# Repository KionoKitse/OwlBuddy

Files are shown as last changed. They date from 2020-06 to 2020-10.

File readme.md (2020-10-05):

### Description  
P09_00_00 OwlBuddy
This project is a simple modify but not repurpose hack. I'm taking a mechanical owl timer that doesn't work very well and converting it into a digital animatronics timer.  
Features
 * Adjustable timing between 1-60 min
 * Servo motion for head movement
 * Detection of timing adjustment
 * Audio feedback
 * LED strobe beacon
 * Battery powered
 * Charge level monitoring
 * Integrated USB charging
 * Automatic sleep and wakeup

### Notes to user
 * Project documented at https://kionokitse.wordpress.com/owlbuddy
 * In development
 
### Hardware
 * Arduino Pro Mini clone ATmega328 5V
 * Micro servo Tower Pro SG90
 * Micro stepper motor
 * High output LED
 
### Progress log 
 * 2020-06-15 Initial project idea 
 * 2020-06-16 Deciding on features and components
 * 2020-06-16 Ordering components
 * 2020-06-16 Initial design sketches
 * 2020-06-17 Ordering components
 * 2020-06-17 Testing LEDs
 * 2020-06-17 Solder stepper motor
 * 2020-06-17 CAD design
 * 2020-06-17 Gear train 
 * 2020-07-04 Redesign CAD P09_00_01
 * 2020-07-04 Start writing software
 * 2020-07-13 Finished 3D printing main components
 * 2020-07-13 Got the VCC readings from the pro mini
 * 2020-07-13 Modify servo for continuous rotation 3.3kOhm resistors
 * 2020-07-13 Testing drive servo with low battery (didn't work)
 * 2020-07-13 Testing direct drive with Arduino pins for the servo motor (didn't work)
 * 2020-07-13 Possible to drive motor using battery leads
 * 2020-07-13 Remove H bridge from SG90 (117L 929 datasheet not found)
 * 2020-07-13 Mapping H bridge pins from SG90
 * 2020-07-13 Modify owl base to accept mini USB adapter
 * 2020-07-14 Probing H bridge found working pinout still a couple unknown pins
 * 2020-09-22 Testing hall effect sensor based encoder 
 * 2020-09-22 Hall encoder results look noisy filtering is very difficult maybe need another approach
 * 2020-09-22 Search mode is the best filter mode so far average filter offsets results slightly
 * 2020-09-22 Inconsistent resistance results in some sections moving faster requiring different filter settings
 * 2020-09-22 Should consider adjustable filter settings
 * 2020-09-26 Testing the idea of adding magnets to the internal gears of the servo
 * 2020-09-27 Testing using metal rods instead of magnets in internal gears
 * 2020-09-27 Tests worked but the process damages the gears not a (feasible option)
 * 2020-09-27 Revisiting the two potentiometer design with trace reinforcement
 * 2020-09-29 Testing dual pot results seem promising
 * 2020-09-29 For the dual pot design I'm noticing when pin A0 is floating it closely resembles pin A1 (not floating) but with more variance
 
### What's next
 * Write a filter to sort out which potentiometer to read from
 * Test wake up from sleep using potentiometer
 * Design layout
 * Test pro mini pins
 * Need to reduce the battery until I can find the min voltage that will drive this project
 
### Function
 * Hardware is asleep 
 * User sets owl time
 * Moving the head will trigger the wakeup command (maybe I need a switch here)
 * Arduino checks the battery voltage if the voltage is low the LED will blink rapidly
 * Timer waits for a few seconds before reading the potentiometer 
 * Timer reads time value
 * Beacon is activated for a few seconds
 * Drive motor goes back to zero then negative whatever value was put include
 * Drive motor goes back to set value
 * Beacon is activated again once the timer starts
 * Arduino goes to sleep
 * Arduino wakes up and moves the drive motor every minute towards zero
 * Arduino also remembers the last set value
 * If the user adjusts the time while the timer is activated the timer will adjust the time accordingly and blink the LED to acknolegde
 * Once the timer goes to zero owl moves 180 then -180 twice before returning to zero
 * During this time the beacon is activated
 * Afterwards the Arduino goes to sleep
 
### Notebook
 * Battery source Li-Po, Li-ion, or Ni-Mh. Ni-Mh has a similar capacity to Li-ion and weight isn't an issue. I already have these batteries and a simple USB charger for them. Size is a little big but it can fit more or less.  
 
 * Sum of squares function that seems to work well https://www.thoughtco.com/sum-of-squares-formula-shortcut-3126266
 * Direct control of mini stepper motor			https://www.youtube.com/watch?v=MaByP2w_vtA
 * Idea for slip ring power for LED strobe		https://gizmoplans.com/product/wind-turbine-slip-rings/
 * Interesting page on li-po charging			https://electronics-project-hub.com/arduino-lithium-ion-battery-charger/
 * CAD for SG90 Servo							https://www.thingiverse.com/thing:787942
 * Putting Arduino to sleep with watchdog		https://learn.adafruit.com/low-power-wifi-datalogging/power-down-sleep
 * Adjust VCC pin reading (didn't use)    		https://forum.arduino.cc/index.php?topic=435065.0 
 * Use VCC pin to read voltage		        	https://provideyourown.com/2012/secret-arduino-voltmeter-measure-battery-voltage/
 
### Next Blog Post
2020-09-29 <font color="63C0EC"><b>P09_00_00 Dual pot design</b></font>
Currently the big sticking point of this project is determining and controlling the head position. I have an SG90 servo that is directly coupled to the head and fixed to the body. I want the head to be able to rotate 360 degrees to allow the user to set a time between 1-60 min. The SG90 servo is only rated to 180 degrees of rotation so I've removed the limits. This allows me to drive the servo as essentially a gear head motor but removes the feedback loop. I've tried a lot of different ideas from hall effect sensors to pulse counting and stacked potentiometers. What I'm doing now is that stack potentiometer idea again. It was one of the first ideas I tried but I noticed that after a few days the potentiometers started bugging out. After disassembly I noticed that the wiper had worn down traces in the sections of the potentiometers that it was not designed to be in. The silver traces did not have any protection against the mechanical abrasion of the wiper. 
>>>IMAGE<<<
The idea was abandoned because I did not see any good way to prevent this from happening and still get continuous rotation. After a lot of trying other stuff it seemed that the dual potentiometer idea was the only idea that had shown some promise. Revisiting the idea I decided that maybe the best option was to protect the traces. For this, I've decided to use a bit of super glue to lay down a protective layer over the silver traces. I'm not sure how well this will stand up to the repeated abrasion but I'm keen to see if it will work. Here is an image of the dual potentiometer I've put together. The two potentiometers have their wipers in opposing positions so when one potentiometer is in the invalid range the other will be in it's valid range.
>>>IMAGE<<< 
<font color="63C0EC">Category:</font> Engineering
<font color="63C0EC">Tags:</font> Animatronics, Arduino, Engineering, Mechatronics, P09_00_00, Timer
<a href="https://kionokitse.wordpress.com/owlbuddy/">Project Page</a>

2020-09-29 <font color="63C0EC"><b>P09_00_00 Dual pot output</b></font>
Recently I had a chance to test the new dual potentiometer design. The results are looking promising but not quite what I had been expecting. One of the effects of coating the traces in super glue is that they are no longer conductive. This is a good thing because if it was conductive, the power would short between the contacts. I hadn't thought of that but note to self: super glue is non-conductive. The other effect that was unexpected is that it seems that a floating pin (no signal) will mirror a non-floating pin on the Arduino. I'm not sure under what cases this is true but in my case it was. On my setup I had A0 reading potentiometer A (PotA) and A1 reading potentiometer B (PotB). When PotA was in the invalid region and thus acting as a floating pin I noticed that it mirrored the results seen on PotB. The same happens if PotB is in the invalid region and PotA is in the valid region. Originally I though that maybe I had some sort of short that was connecting the output of PotA and PotB but that was not the case. If I move PotA into the valid region and transverse the valid region on PotB it's clear to see that there is no connection between them. In effect, this means that I will always be reading two values from the potentiometers that on the surface look valid. Here is a graph of two periods or 520 degrees of rotation.
>>>IMAGE<<<
It's not clear which sensor is in the valid region and which sensor is in the invalid region. One thing I noticed though was that it was possible to distinguish the two based on the amount of noise in the data. If a pin is floating then it's likely that all the data that is coming in in noise. Not quite what is happening here but with noise there tends to be quite a lot of variance compare to a set pin. When I look closer and the signal data it's easy to see which sensor is actually in the valid region.
>>>IMAGE<<<
>>>IMAGE<<<
<font color="63C0EC">Category:</font> Engineering
<font color="63C0EC">Tags:</font> Animatronics, Arduino, Engineering, Mechatronics, P09_00_00, Timer
<a href="https://kionokitse.wordpress.com/owlbuddy/">Project Page</a>

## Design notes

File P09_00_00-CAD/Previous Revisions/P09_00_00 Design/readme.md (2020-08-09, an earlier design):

### Overview:
__Name:__ P09_00_00 CAD Design <br>
__Software Version:__ FreeCAD 0.15 <br>
__Notes:__ Design superseded by P09_00_01 <br>
__Comments:__ This design did not work well. The gears were not supported well and caused pinching which was too much friction for the servo. Additionally the design was somewhat restrictive in only being able to rotate 360 degrees.

### Description:
This design is the first iteration of P90_00_00. It calls for one SG90 servo to control the owl head movement and one micro stepper motor for the beacon motion. With additional gearing the servo action is extended to a full 360 degrees of motion. The timer setting are directly read from the servo potentiometer.  

### Files:
 * __Assembly:__ The parts aligned to check for interference
 * __BeaconLens:__ The red lens that covers the LED on top of the owl's head
 * __LEDMount:__ The mounting part that mates the stepper motor with the LED
 * __StepperMast:__ Part that holds the stepper motor vertically and mates to the BeaconBase to ensure the mast is centered
   * R2: Redesigned with a hallow center for passing wires though the BeaconBase and DriveGear  
 * __BeaconBase:__ Platform for beacon in the owl timer head
   * R2: Design modified for attaching directly to the drive gear. R1 design was flawed
 * __DriveGear:__ Main drive gear for owl head motion connected to servo motor in owl body
   * R2: Reduced the gear module
 * __ServoGear:__ Gear that is placed on servo head to drive the head action
   * R2: Reduced the gear module
 * __MainFrame:__ The main frame component where the servo is attached to the owl body
   * R2: Redesigned with the servo motor at an angle for better access and better component sizing
 * __DriveRetainer:__ Part for retaining the drive gear in the MainFrame
   * R2: Modified sizing on the DriveRetainer
 * __BottomPlate:__ Support plate for drive servo and other electronics. Goes in the bottom half of owl timer
   * R2: Simplified the design for less space
   * R3: Resized hole for servo. Fit is much better

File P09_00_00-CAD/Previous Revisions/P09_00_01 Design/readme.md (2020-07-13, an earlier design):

Name: P09_00_01 CAD Design
Software Version: FreeCAD 0.15
Notes: Design superseded by P09_00_02
Comments: The stepper motor was not powerful enough to rotate the LED with the lead wires attached. Other design features worked well and were kept.

Description:
This design is the second iteration of P90_00_00. It calls for one SG90 servo to control the owl head movement and one micro stepper motor for the beacon motion. The SG90 servo is modified for continuous rotation and is directly connected to the owl head. The continuous rotation modification disallows for the usage of the SG90 potentiometer so a DIY one is designed to fit with the owl body and head section. The potentiometer makes use of 26GA nichrome wire which will also be needed.

Assembly: The parts aligned to check for interference
BeaconLens: The red lens that covers the LED on top of the owl's head (unmodified since P09_00_00)
LEDMount: The mounting part that mates the stepper motor with the LED
StepperMast: Part that holds the stepper motor vertically and mates to the BeaconBase to ensure the mast is centered (unmodified since P09_00_00R2)
BeaconBase: Top part of the potentiometer and base for stepper mast. Placed inside of owl head 
ServoHead: Attachment part that mates the servo to the top part of the potentiometer 
MainFrame: The main frame component where the servo is attached to the owl body. Also comprises of the bottom half of the potentiometer
BottomPlate: Support plate for drive servo and other electronics. Goes in the bottom half of owl timer (unmodified since P09_00_00R3)

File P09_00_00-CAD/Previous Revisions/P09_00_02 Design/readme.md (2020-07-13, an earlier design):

Name: P09_00_02 CAD Design
Software Version: FreeCAD 0.15 and FreeCAD 0.18* 
Notes: Design superseded by P09_00_03
Comments: Worm gear design worked but seemed to be somewhat unreliable. Additionally the gear ratio wasn't high enough, resulting in a beacon that spun too fast. Gear noise was almost as loud as SG90 under normal conditions.

Description:
This design is the second third iteration of P90_00_00. It calls for one SG90 servo to control the owl head movement and another SG90 motor to drive the worm gear for the beacon motion. The SG90 servo is modified for continuous rotation and is directly connected to the owl head. The continuous rotation modification disallows for the usage of the SG90 potentiometer so a DIY one is designed to fit with the owl body and head section. The potentiometer makes use of 26GA nichrome wire which will also be needed. For the worm gear drive train a motor is removed from a SG90 and mated to the worm gear. The worm gear is supported by a 2mm axle shaft and drives a worm wheel that is mated to the shell of a bic pen. The LED mount is installed on the bic pen shaft and wires to the LED are passed through the hollow shaft. Power to the LED is supplied by a DIY slip ring making use of nichrome wires as the the slip ring brushes.

Assembly: The parts aligned to check for interference
BeaconLens: The red lens that covers the LED on top of the owl's head (unmodified since P09_00_00)
LEDMount: The mounting part that mates the pen shaft with the LED
GearboxTop*: Top part of the worm gear drive train enclosure. Also contains the mounting points for the slip ring brushes
WormWheel*: Worm wheel that mates with the worm gear
WormGear*: Worm gear that mates to the SG90 motor and drives the worm wheel
GearboxBottom*: Bottom part of the worm gear drive train enclosure
BeaconBase: Top part of the potentiometer and base for stepper mast. Placed inside of owl head (unmodified since P09_00_01R1)
ServoHead: Attachment part that mates the servo to the top part of the potentiometer (unmodified since P09_00_01R1)
MainFrame: The main frame component where the servo is attached to the owl body. Also comprises of the bottom half of the potentiometer (unmodified since P09_00_01R1)
BottomPlate: Support plate for drive servo and other electronics. Goes in the bottom half of owl timer (unmodified since P09_00_00R3)
SG90ServoMotor: Motor removed from SG90 (modeled for fit)
*Modeled with FreeCAD 0.18

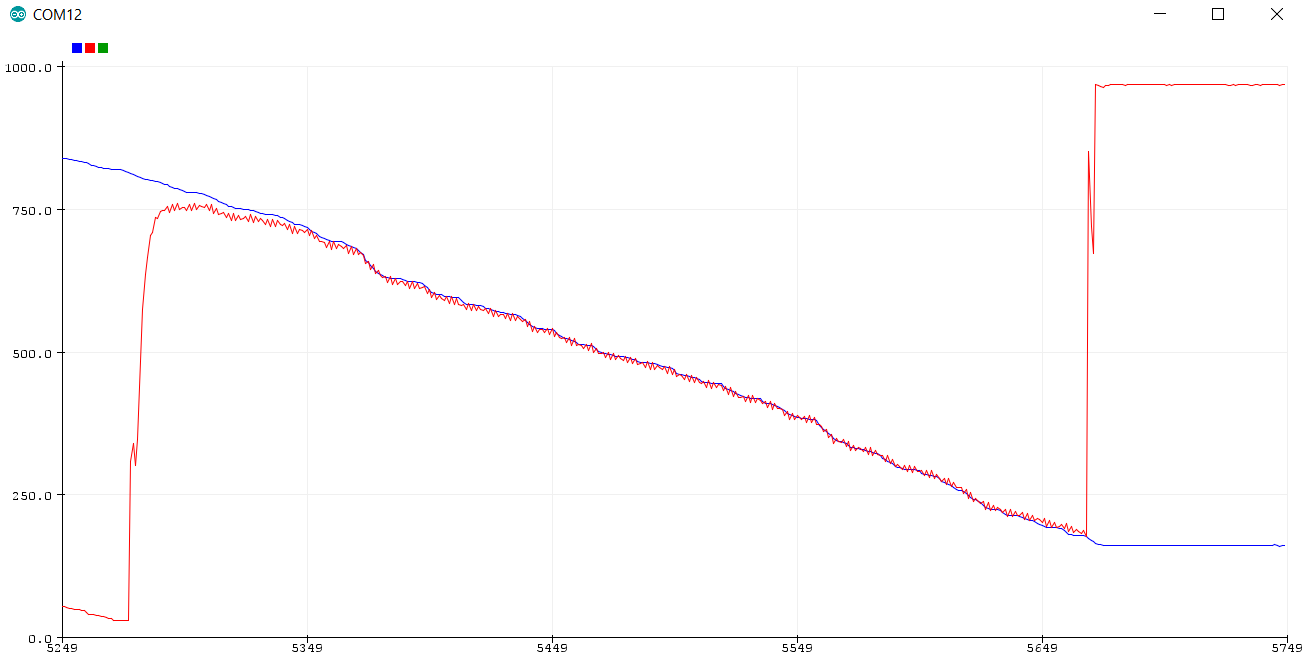
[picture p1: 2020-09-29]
P09_00_00-Web/a.png

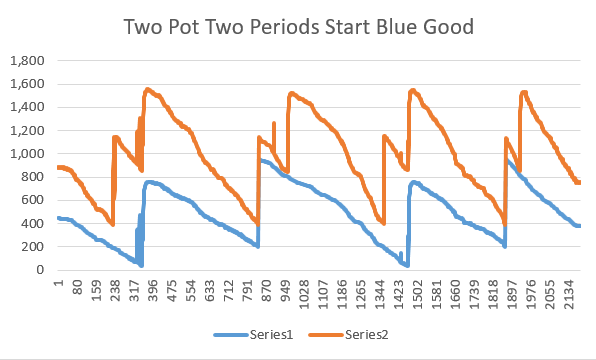
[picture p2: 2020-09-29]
P09_00_00-Web/c.png

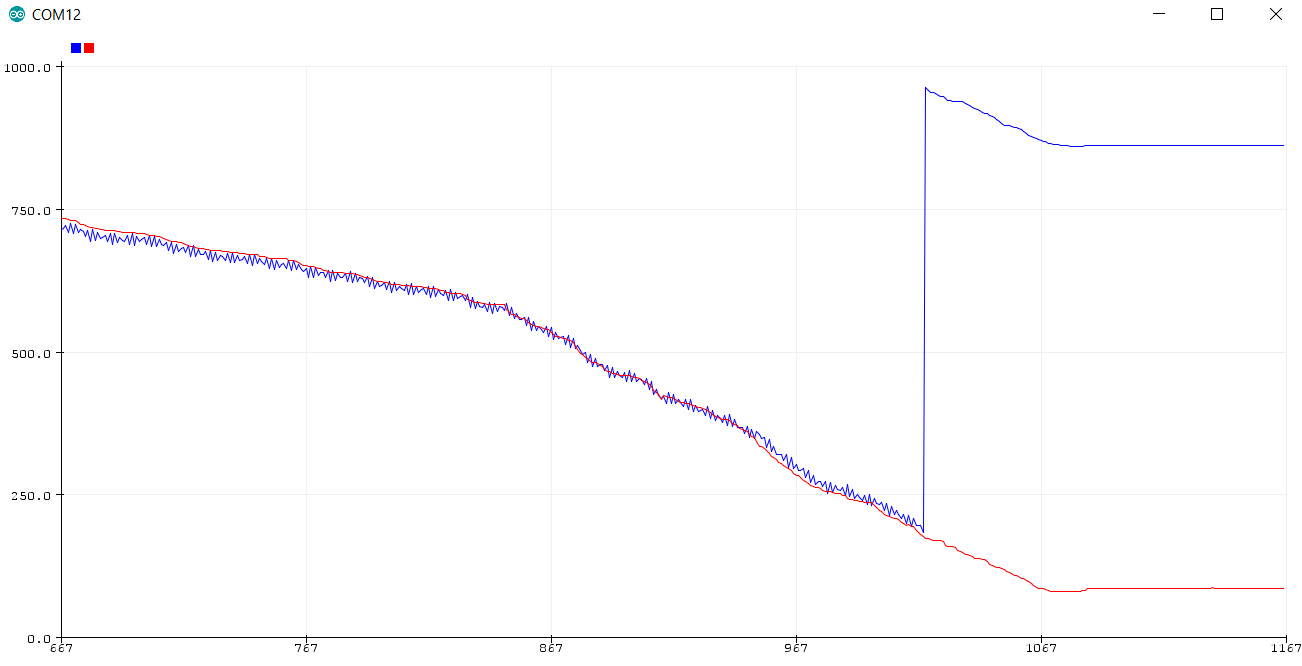
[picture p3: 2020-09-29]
P09_00_00-Web/b.png

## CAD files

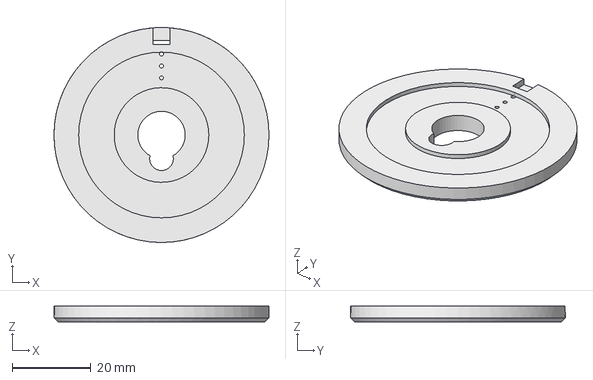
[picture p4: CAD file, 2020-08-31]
P09_00_00-CAD/P09_00_05R1MainFrame.FCStd
54.5 x 54.5 x 4.00 mm

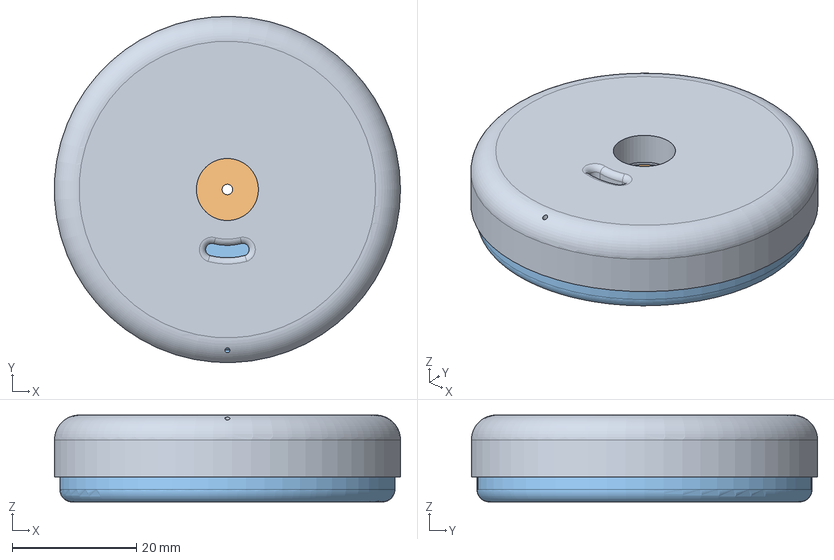
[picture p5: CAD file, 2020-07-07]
P09_00_00-CAD_R1/P09_00_01Assembly.FCStd
55.8 x 55.8 x 14.0 mm
Top
Middle
Bottom

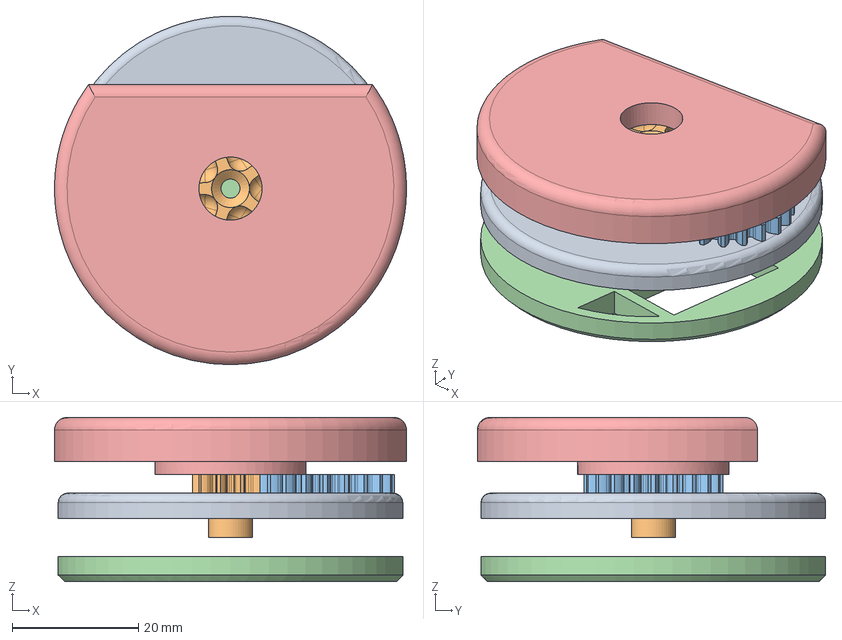
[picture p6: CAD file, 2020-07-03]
P09_00_00-CAD_R1/Po9_00_00R2Assembly.FCStd
55.8 x 55.2 x 26.0 mm
MainFrame
DriveGear
ServoGear
BottomPlate
BeaconBase

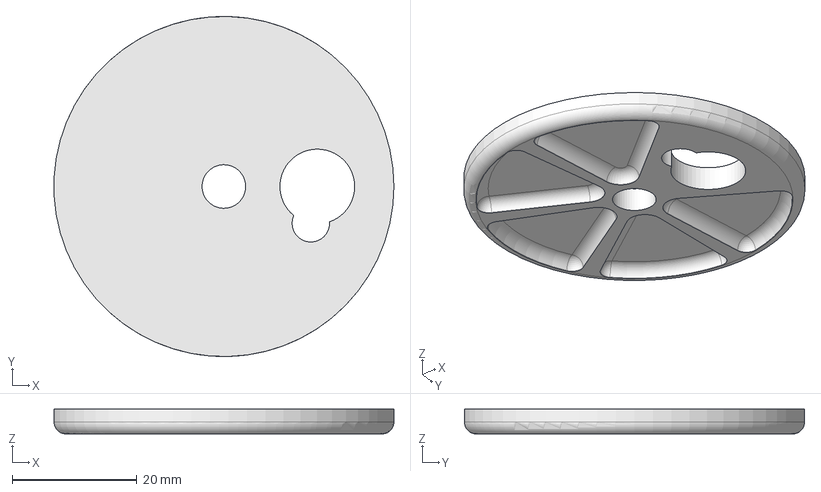
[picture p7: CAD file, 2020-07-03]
P09_00_00-CAD_R1/P09_00_00R2MainFrame.FCStd
54.6 x 54.6 x 4.00 mm

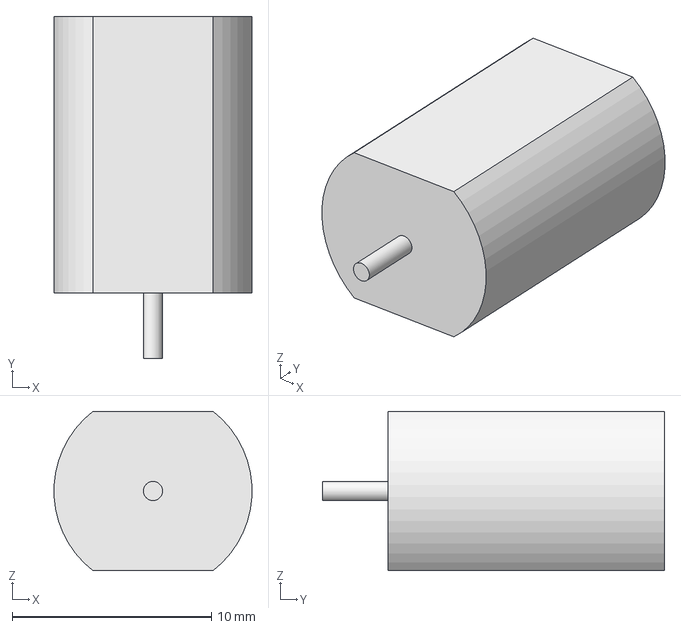
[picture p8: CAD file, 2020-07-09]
P09_00_00-CAD/Generic Parts/Part_SG90ServoMotor.FCStd
9.93 x 17.2 x 8.00 mm

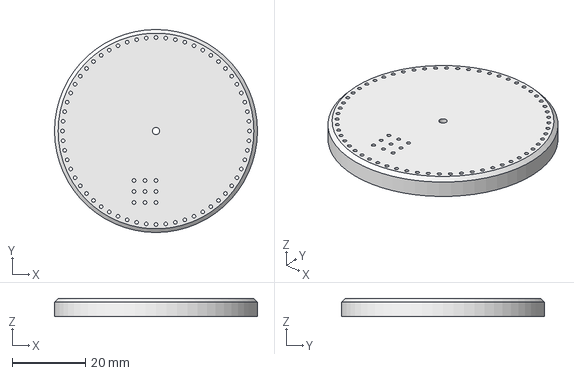
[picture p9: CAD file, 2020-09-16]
P09_00_00-CAD/P09_00_05R3EncoderTop.FCStd
55.4 x 55.4 x 5.00 mm

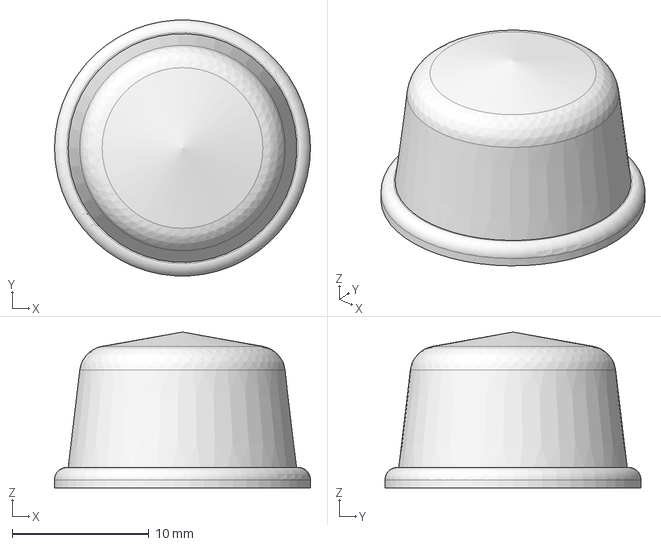
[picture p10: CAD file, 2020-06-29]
P09_00_00-CAD_R1/Done/P09_00_00R1BeaconLens.FCStd
18.7 x 18.7 x 11.4 mm

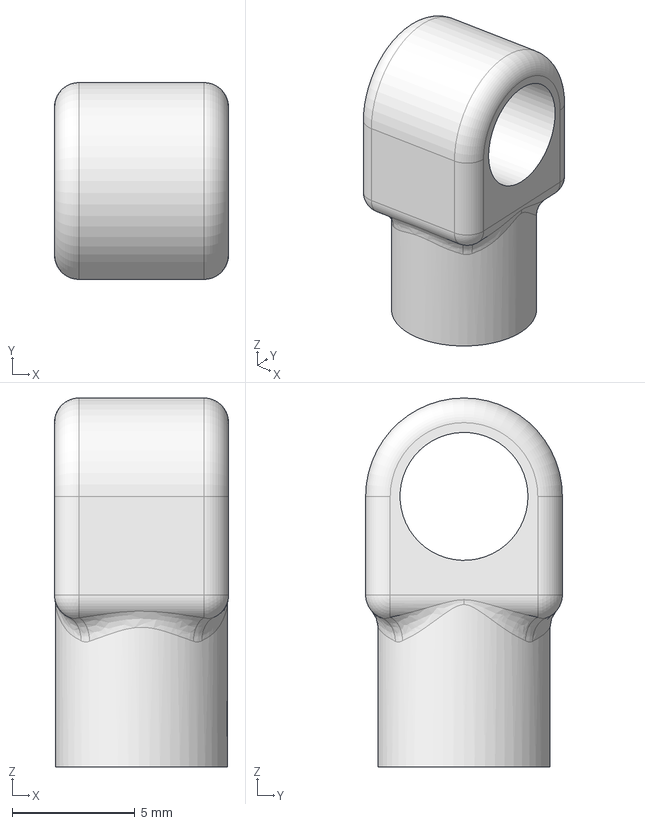
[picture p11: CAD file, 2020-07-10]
P09_00_00-CAD_R1/P09_00_03LEDMount.FCStd
7.08 x 8.00 x 15.0 mm

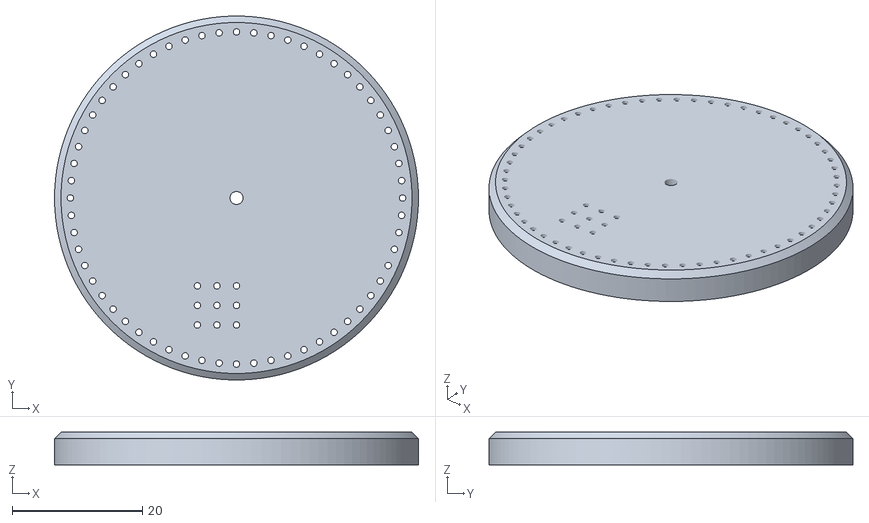
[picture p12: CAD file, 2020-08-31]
P09_00_00-CAD/a.stl
55.9 x 55.9 x 5.00

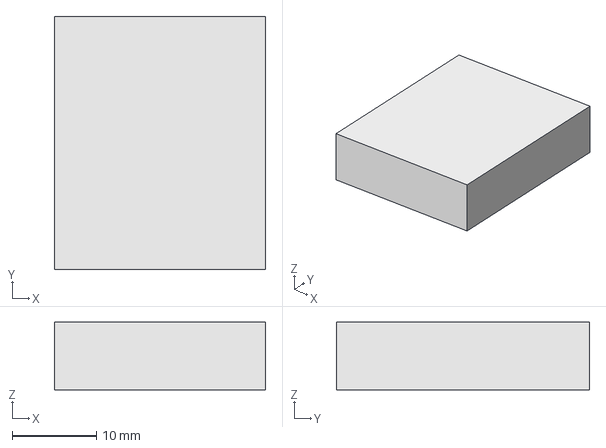
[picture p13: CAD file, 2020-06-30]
P09_00_00-CAD/Generic Parts/Part_LiPo.FCStd
25.0 x 30.0 x 8.00 mm

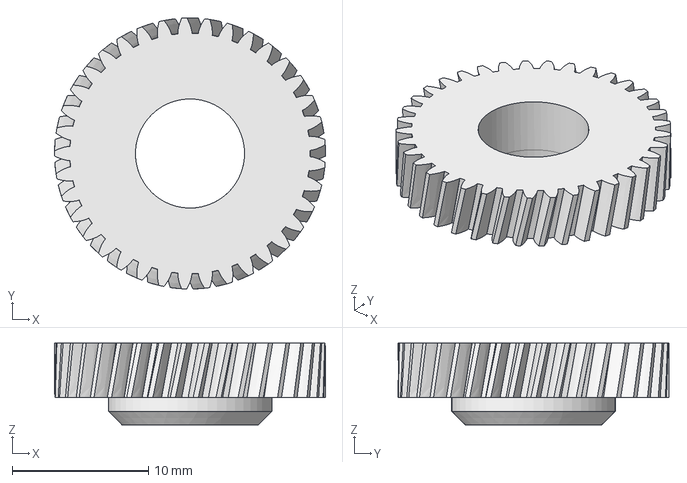
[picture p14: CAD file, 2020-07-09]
P09_00_00-CAD_R1/P09_00_02R1WormWheel.FCStd
19.9 x 19.9 x 6.00 mm

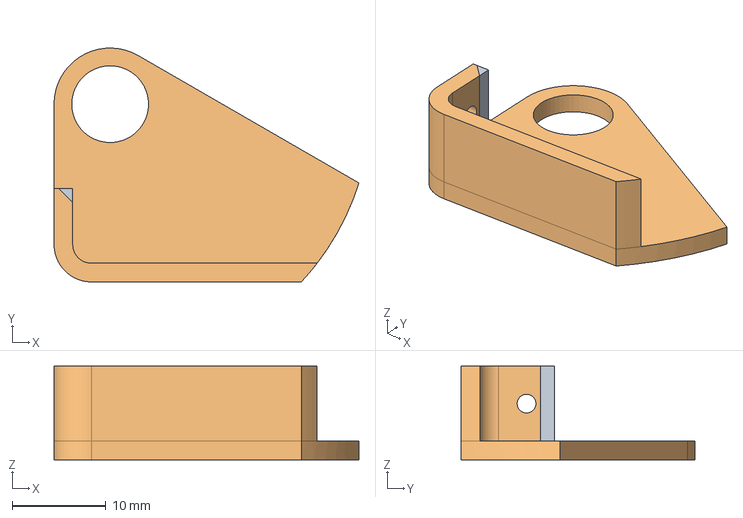
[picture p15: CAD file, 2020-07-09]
P09_00_00-CAD_R1/P09_00_02R1GearboxBottom.FCStd
32.6 x 25.0 x 10.0 mm

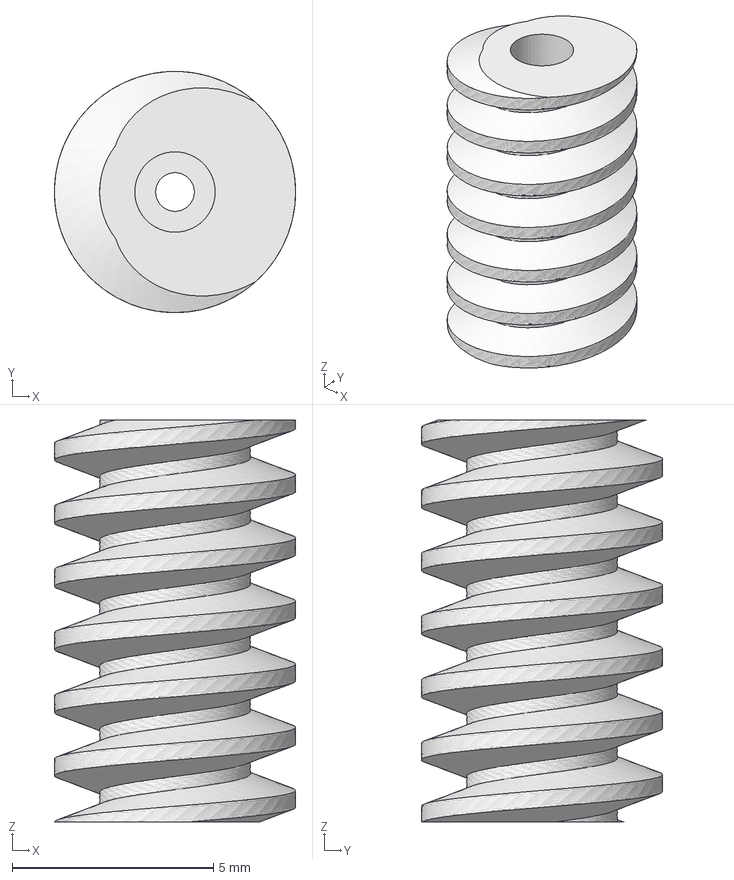
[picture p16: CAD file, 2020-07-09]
P09_00_00-CAD_R1/P09_00_02R1WormGear.FCStd
6.00 x 6.00 x 10.00 mm

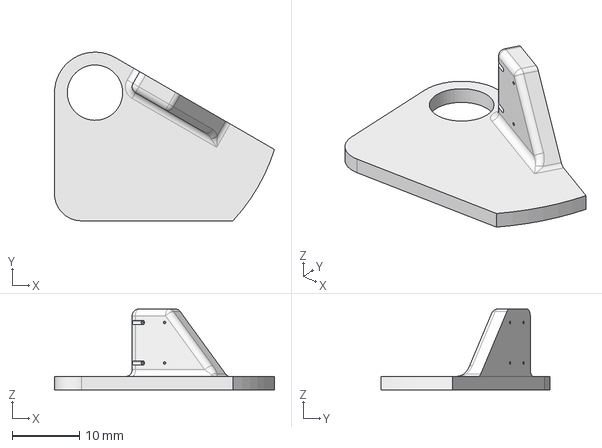
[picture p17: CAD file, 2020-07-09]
P09_00_00-CAD_R1/P09_00_02R1GearboxTop.FCStd
32.6 x 25.0 x 12.0 mm

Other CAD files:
P09_00_00-CAD/P09_00_04R1MainFrame.FCStd
P09_00_00-CAD/P09_00_05R1EncoderTop.FCStd
P09_00_00-CAD/bb.stl
P09_00_00-CAD/P09_00_04R1Encoder.FCStd
P09_00_00-CAD/P09_00_03ALEDMount.FCStd
P09_00_00-CAD/P09_00_03R1BeaconBase.FCStd
P09_00_00-CAD/P09_00_03R1SlipRing.FCStd
P09_00_00-CAD/P09_00_04R1EncoderTop.FCStd
P09_00_00-CAD/Previous Revisions/P09_00_00 Design/P09_00_00R1BeaconBase.FCStd
P09_00_00-CAD/Previous Revisions/P09_00_00 Design/P09_00_00R1BottomPlate.FCStd
P09_00_00-CAD/Previous Revisions/P09_00_00 Design/P09_00_00R1DriveGear.FCStd
P09_00_00-CAD/Previous Revisions/P09_00_00 Design/P09_00_00R1DriveRetainer.FCStd
P09_00_00-CAD/Previous Revisions/P09_00_00 Design/P09_00_00R1LEDMount.FCStd
P09_00_00-CAD/Previous Revisions/P09_00_00 Design/P09_00_00R1MainFrame.FCStd
P09_00_00-CAD/Previous Revisions/P09_00_00 Design/P09_00_00R1ServoGear.FCStd
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

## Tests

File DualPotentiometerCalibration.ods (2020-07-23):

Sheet: Sheet1
0 | 2 | 2505 | 60
1 | 2 | 2482 | 59
2 | 2 | 2462 | 58 | 30
3 | 2 | 2433 | 57
4 | 2 | 2408 | 56
5 | 2 | 2375 | 55
6 | 2 | 2337 | 54
7 | 2 | 2308 | 53
8 | 2 | 2278 | 52
9 | 2 | 2247 | 51
10 | 2 | 2207 | 50
11 | 2 | 2189 | 49
12 | 1 | 1970 | 48
13 | 1 | 1953 | 47
14 | 1 | 1928 | 46
15 | 1 | 1898 | 45
16 | 1 | 1874 | 44
17 | 1 | 1852 | 43
18 | 1 | 1825 | 42
19 | 1 | 1797 | 41
20 | 1 | 1773 | 40
21 | 1 | 1745 | 39
22 | 1 | 1718 | 38
23 | 1 | 1691 | 37
24 | 1 | 1667 | 36
25 | 1 | 1638 | 35
26 | 1 | 1614 | 34
27 | 1 | 1591 | 33
28 | 1 | 1559 | 32
29 | 1 | 1517 | 31
30 | 1 | 1486 | 30
31 | 1 | 1447 | 29
32 | 1 | 1425 | 28
33 | 1 | 1397 | 27
34 | 1 | 1365 | 26
35 | 1 | 1338 | 25
36 | 1 | 1303 | 24
37 | 1 | 1277 | 23
38 | 1 | 1252 | 22
39 | 1 | 1223 | 21
40 | 1 | 1184 | 20
41 | 1 | 1156 | 19
42 | 1 | 1130 | 18
43 | 1 | 1110 | 17
44 | 1 | 1086 | 16
45 | 1 | 1059 | 15
46 | 1 | 1029 | 14
47 | 2 | 2882 | 13
48 | 2 | 2858 | 12
49 | 2 | 2831 | 11
50 | 2 | 2800 | 10
51 | 2 | 2774 | 9
52 | 2 | 2751 | 8
53 | 2 | 2722 | 7
54 | 2 | 2697 | 6
55 | 2 | 2673 | 5
56 | 2 | 2644 | 4
57 | 2 | 2619 | 3
58 | 2 | 2593 | 2
59 | 2 | 2562 | 1
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

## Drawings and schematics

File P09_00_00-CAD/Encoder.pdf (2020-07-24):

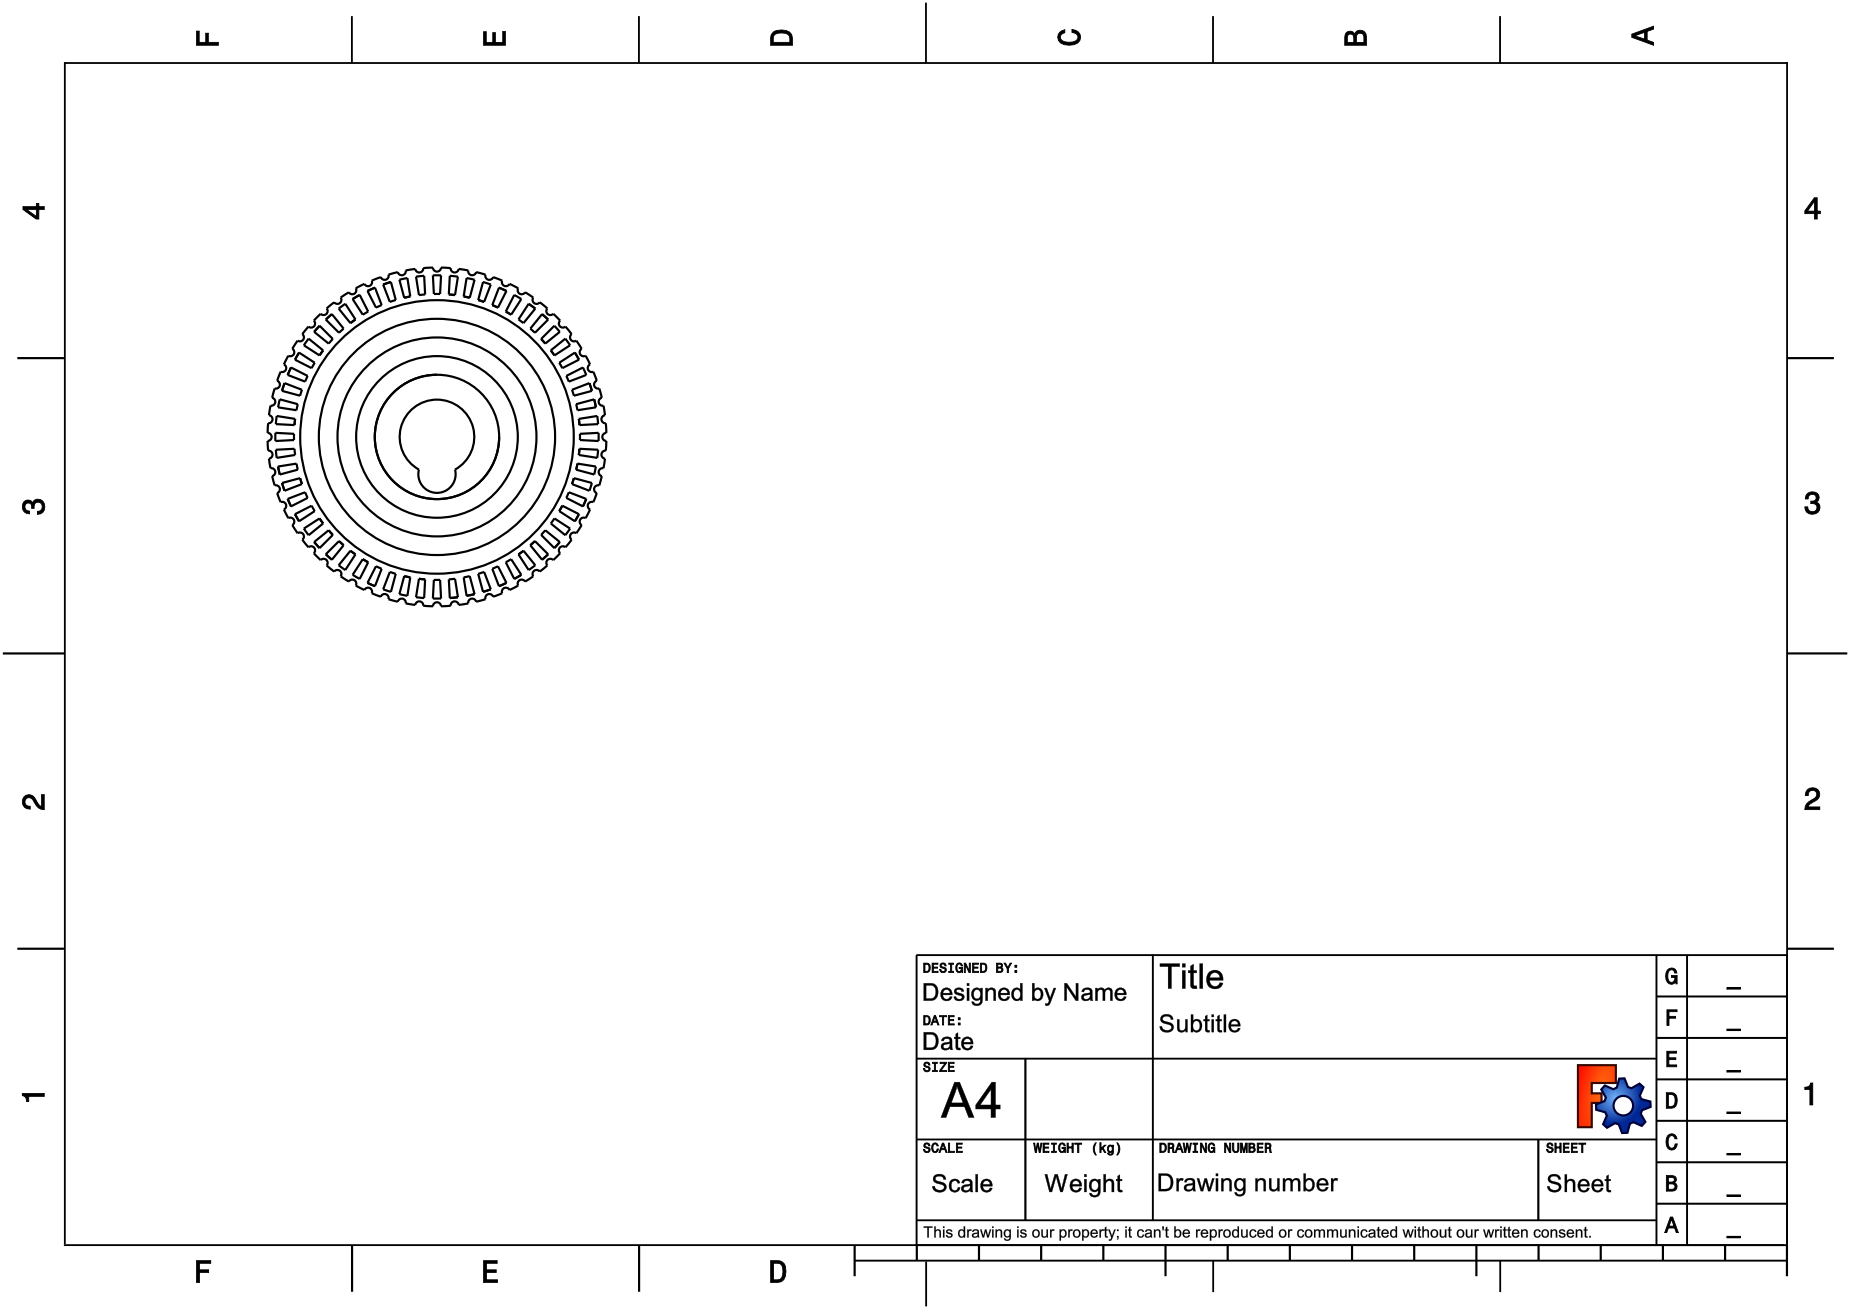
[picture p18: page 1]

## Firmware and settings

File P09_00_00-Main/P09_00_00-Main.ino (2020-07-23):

/*
   P09_00_00-Main
   Project: P09_00_00 OwlBuddy
   
   Notes:
 * Working on switch cases
 * Need to fill in code for MoveToZeroFine 
 * 

   Connections
   GND   - Servo potentiometer GND
   Pin02 - Servo potentiometer output
*/

//Sleep mode (interrupt)
#include <avr/sleep.h>
#define WakePin 2   //Pin to indicate when the timer has been activated

//Settings
long MinVoltage = 3000;   //Voltage level (mV) to trigger low voltage warning dead at 2.8V
int SetTimeDelay = 3000;  //Amount of time to wait before setting the timer
byte ZeroTolerance = 8;   //Tolerance on positioning of owl head at zero
byte ZeroPos = 542; //InvalidSensorA[] = {145, 939} -> ((939-145)/2)+145 = 542
 
//Define pins
#define LED         13  //Beacon LED
#define SensorPWR     9  //Potentiometer power
#define SensorA      A0  //Blue wire
#define SensorB      A1  //White wire //interrupt
#define DriveA       10  //Drive motor H bridge White 3
#define DriveB       11  //Drive motot H bridge Blue 4

//Global variables (General)
byte CaseMode;
int SetTime;
byte i;
bool Sleeping;
byte SensorNumber;
int  SensorValue;

//Global variables (Potentiometer Functions)
int ValSensorA;
int ValSensorB;
bool StableA;
bool StableB;

//Global variables (Battery Control Functions)
long BatteryVoltage;
bool LowBattery;

//Potentiometer Calibration
int ValidSensorA[] = {1020, 1990};
int ValidSensorB[] = {2020, 2990};
double Slope = -0.03472536;
double Intercept = 87.37676476;
int OffsetSensorA = 170;
byte WrapAroundVal;


void setup() {
  //Serial
  Serial.begin(9600);
  Serial.println("Setup");

  //Check battery status
  CheckBattery();

  //Sleep mode (interrupt)
  pinMode(WakePin,INPUT_PULLUP);  //Set internal pull up resistor

  //Set default case
  CaseMode = 0;

  //Apply sensor offset
  ValidSensorA[0] = ValidSensorA[0]+OffsetSensorA;
  ValidSensorA[1] = ValidSensorA[1]+OffsetSensorA;

  //General pin setup
  pinMode(LED,OUTPUT);
  pinMode(SensorPWR,OUTPUT);

  //Blink at setup done
  for(int i=0; i<5; i++)
  {
    digitalWrite(LED,HIGH);
    delay(100);
    digitalWrite(LED,LOW);
    delay(100);
  }
}



void loop() {
  switch (CaseMode) 
  {
    case 1:
      //Serial.println("Owl is awake getting set time");

      /*
      //Check for low battery
      CheckBattery();

      //Delay for setting the time 
      //Note: If low battery a delay is already applied
      if (!LowBattery)
      {
        delay(SetTimeDelay); 
      }
      */
      
      //Get the time value based on unknown position
      GetUnkownPos();
      //SetTime = Pos2Time(SensorValue);
      //Serial.print("Set Timer: ");
      //Serial.println(SetTime);
      
      //CaseMode = 2;
      break;
    case 2:
      Serial.println("Sleep until time is up");
      Sleeping = true;
      while (Sleeping)
      {
        
      }
      break;
    default: 
      //Serial.println("Sleep until activated");
      GetUnkownPos();
      //Move the head to the zero position
      //MoveToZeroFine(); //TODO
      
      ActivateSleep();
      CaseMode = 1;
      break;
  }
}

//Function to move owl head to zero 
void MoveToZeroFine()
{
  //Note: Interrupt is on SensorA so using SensorB to set position (Switch in HW)
  bool AtZero = false;

  //Turn on power for potentiometers
  digitalWrite(SensorPWR,HIGH);
  while(!AtZero)
  {
    //Read the sensor
    ValSensorB = analogRead(SensorB);

    //Need to rotate counter clockwise
    if(ValSensorB > (ZeroPos + ZeroTolerance))
    {
      StepMotor(0, 2);
    }
    //Need to rotate clockwise
    else if (ValSensorB < (ZeroPos - ZeroTolerance))
    {
      StepMotor(1, 2);
    }
    //Within nominal range
    else
    {
      AtZero = true;
    }
  }
  digitalWrite(SensorPWR,LOW);
}

//>>>DONE<<<


//Function to step drive motor
void StepMotor(bool Clockwise, int Time)
{
  if(Clockwise)
  {
    digitalWrite(DriveA,LOW);
    digitalWrite(DriveB,HIGH);
    delay (Time);
    digitalWrite(DriveB,LOW);
  }
  else
  {
    digitalWrite(DriveB,LOW);
    digitalWrite(DriveA,HIGH);
    delay (Time);
    digitalWrite(DriveA,LOW);
  }
}

// >> Potentiometer Functions << 
int Pos2Time(int Position) {                  //Convert sensor position to time
  //Calculate time based on position to time equation
  double Time = Slope * Position + Intercept;

  //Round values to an integer
  int Result = round(Time);

  //Check for wrap around values
  if (Result < 0)
  {
    Result = Result + 60;
  }

  return Result;
}
void GetUnkownPos() {                         //Get unknown position
  //Turn sensor on
  digitalWrite(SensorPWR, HIGH);
  delay(2);

  //Get sensor reading
  ValSensorA = analogRead(SensorA) + 1000 + OffsetSensorA;
  ValSensorB = analogRead(SensorB) + 2000;

  //Turn sensor off
  digitalWrite(SensorPWR, LOW);

  Serial.print(ValSensorA);
  Serial.print(",");
  Serial.print(ValSensorB);
  Serial.print(": ");

  //Check for valid readings
  bool SensorAValid = SensorValid(ValSensorA, ValidSensorA);
  bool SensorBValid = SensorValid(ValSensorB, ValidSensorB);

  //Check reading stability if both readings are valid
  if (SensorAValid && SensorBValid)
  {
    StableA = true;
    StableB = true;
    CheckStable();
    CheckStable();

    //Both readings are actually stable use SensorA
    if (StableA && StableB)
    {
      //Serial.print("Stable ");
      SensorValue = ValSensorA;
      SensorNumber = 1;
    }
    //Sensor B was unstable so use SensorA
    else if (StableA)
    {
      SensorValue = ValSensorA;
      SensorNumber = 1;
    }
    //SensorA was unstable so use SensorB
    else
    {
      SensorValue = ValSensorB;
      SensorNumber = 2;
    }
  }
  //SensorB was unstable so use SensorA
  else if (SensorAValid)
  {
    SensorValue = ValSensorA;
    SensorNumber = 1;
  }
  //SensorA was unstable so use SensorB
  else
  {
    SensorValue = ValSensorB;
    SensorNumber = 2;
  }

  Serial.println(SensorValue);
}
bool SensorValid(int Value, int Limits[2]) {  //Check if sensor reading is valid
  if ((Value > Limits[0]) && (Value < Limits[1]))
  {
    return true;
  }
  return false;
}
void CheckStable() {                          //Check stability of sensors over 10 readings
  //Calculate the sum of 10 measurements
  unsigned int TotalA = 0;
  unsigned int TotalB = 0;
  for (byte i = 0; i < 10; i++)
  {
    //Turn sensor on
    digitalWrite(SensorPWR, HIGH);
    delay(2);

    //Get sensor reading
    ValSensorA = analogRead(SensorA) + 1000 + OffsetSensorA;
    ValSensorB = analogRead(SensorB) + 2000;

    //Turn sensor off
    digitalWrite(SensorPWR, LOW);

    //Calculate the sum
    TotalA = TotalA + ValSensorA;
    TotalB = TotalB + ValSensorB;
  }

  //Calculate theoretical total
  unsigned int TotalATheo = 10 * ValSensorA;
  unsigned int TotalBTheo = 10 * ValSensorB;

  //Determine how much the actual total and the theoretical total differ
  int DeltaA = TotalATheo - TotalA;
  int DeltaB = TotalBTheo - TotalB;
  DeltaA = abs(DeltaA);
  DeltaB = abs(DeltaB);

  //Determine which reading is valid
  if (DeltaA > 11)
  {
    StableA = false;
  }
  if (DeltaB > 11)
  {
    StableB = false;
  }
}

// >> Battery Control Functions <<
void CheckBattery(){                          //Check for low battery
  //Get the battery voltage
  BatteryVoltage = ReadVcc();
  Serial.println(BatteryVoltage);

  //Check for low power
  if (BatteryVoltage < MinVoltage)
  {
    LowBattery = true;

    //Blink LED to indicate low battery
    for(i=0; i<8; i++)
    {
      digitalWrite(LED,HIGH);
      delay(200);
      digitalWrite(LED,LOW);
      delay(200);
    }
  }
  else
  {
    LowBattery = false;
  }
}
long ReadVcc() {                              //Calculate Vcc (in mV)
  // Read 1.1V reference against AVcc
  // set the reference to Vcc and the measurement to the internal 1.1V reference
  #if defined(__AVR_ATmega32U4__) || defined(__AVR_ATmega1280__) || defined(__AVR_ATmega2560__)
    ADMUX = _BV(REFS0) | _BV(MUX4) | _BV(MUX3) | _BV(MUX2) | _BV(MUX1);
  #elif defined (__AVR_ATtiny24__) || defined(__AVR_ATtiny44__) || defined(__AVR_ATtiny84__)
    ADMUX = _BV(MUX5) | _BV(MUX0);
  #elif defined (__AVR_ATtiny25__) || defined(__AVR_ATtiny45__) || defined(__AVR_ATtiny85__)
    ADMUX = _BV(MUX3) | _BV(MUX2);
  #else
    ADMUX = _BV(REFS0) | _BV(MUX3) | _BV(MUX2) | _BV(MUX1);
  #endif  

  delay(2); // Wait for Vref to settle
  ADCSRA |= _BV(ADSC); // Start conversion
  while (bit_is_set(ADCSRA,ADSC)); // measuring

  uint8_t low  = ADCL; // must read ADCL first - it then locks ADCH  
  uint8_t high = ADCH; // unlocks both

  long result = (high<<8) | low;

  result = 1142437L / result; // Calculate Vcc (in mV); 1125300 = 1.1*1023*1000
  return result; // Vcc in millivolts
}

// >> Sleep Functions <<
void ActivateSleep(){                         //Activate the sleep mode (interrupt)
  Serial.println("ActivateSleep");
  delay(200);
    
  //Enable sleep mode
  sleep_enable();

  //Sleep mode settings
  attachInterrupt(0, WakeUp, LOW); //0 = Pin02
  set_sleep_mode(SLEEP_MODE_PWR_DOWN);

  //Go to sleep
  sleep_cpu();
}
void WakeUp(){                                //Interrrupt routine
  sleep_disable();//Disable sleep mode
  detachInterrupt(0); //0 = Pin02
}

// >> Calibration  Functions <<
void LineFitLSR(double Data[60][2], double Equation[2], byte Count){    //Least squares line fit
  double sum_x = 0;
  double sum_y = 0;
  double sum_x2 = 0;
  double sum_y2 = 0;
  double sum_xy = 0;

  for (byte i=0; i<Count; i++)
    {
    sum_x += Data[i][0];
    sum_y += Data[i][1];
    sum_x2 += Data[i][0] * Data[i][0];
    sum_y2 += Data[i][1] * Data[i][1];
    sum_xy += (Data[i][0] * Data[i][1]);
  }
  
  Equation[0] = (Count * sum_xy - sum_x * sum_y) / (Count * sum_x2 - sum_x * sum_x);
  Equation[1] = (sum_x2 * sum_y - sum_x * sum_xy) / (Count * sum_x2 - sum_x * sum_x);

  /*
  //Print results
  Serial.print(sum_x);
  Serial.print(",");
  Serial.print(sum_y);
  Serial.print(",");
  Serial.print(sum_x2);
  Serial.print(",");
  Serial.print(sum_y2);
  Serial.print(",");
  Serial.println(sum_xy);
  Serial.print(Equation[0]);
  Serial.print(",");
  Serial.println(Equation[1]);
  */
} 
void Calibration() {                          //Calibration sequence
  //Configure variables
  int PositionTable[60];
  byte SensorTable[60];

  //Start process
  Serial.println("Move to zero position");
  delay(5000);
  for (byte i=0; i<60; i++)
  {
    Serial.print("Move to position: ");
    Serial.println(i);
    delay(5000);

    //Get sensor readings
    GetUnkownPos();
    PositionTable[i] = SensorValue;
    SensorTable[i] = SensorNumber;

    //Flash to indicate readings saved
    digitalWrite(LED,HIGH);
    delay(100);
    digitalWrite(LED,LOW);
  }

  //Sample data
  //int PositionTable[60] = {2505, 2482, 2462, 2433, 2408, 2375, 2337, 2308, 2278, 2247, 2207, 2189, 1970, 1953, 1928, 1898, 1874, 1852, 1825, 1797, 1773, 1745, 1718, 1691, 1667, 1638, 1614, 1591, 1559, 1517, 1486, 1447, 1425, 1397, 1365, 1338, 1303, 1277, 1252, 1223, 1184, 1156, 1130, 1110, 1086, 1059, 1029, 2882, 2858, 2831, 2800, 2774, 2751, 2722, 2697, 2673, 2644, 2619, 2593, 2562};
  //byte SensorTable[60] = {2, 2, 2, 2, 2, 2, 2, 2, 2, 2, 2, 2, 1, 1, 1, 1, 1, 1, 1, 1, 1, 1, 1, 1, 1, 1, 1, 1, 1, 1, 1, 1, 1, 1, 1, 1, 1, 1, 1, 1, 1, 1, 1, 1, 1, 1, 1, 2, 2, 2, 2, 2, 2, 2, 2, 2, 2, 2, 2, 2};

  //Print results - Time, Sensor, Position 
  Serial.println("Calibration values");
  for (byte i = 0; i < 60; i++)
  {
    Serial.print(i);
    Serial.print(",");
    Serial.print(SensorTable[i]);
    Serial.print(",");
    Serial.println(PositionTable[i]);
  }

  //Split data into SensoA and SensorB data
  double XYSensorA[60][2];
  double XYSensorB[60][2];
  byte CountSensorA = 0;
  byte CountSensorB = 0;
  for (byte i = 0; i < 60; i++)
  {
    //SensorA data
    if (SensorTable[i] == 1)
    {
      XYSensorA[CountSensorA][0] = i;
      XYSensorA[CountSensorA][1] = PositionTable[i];
      CountSensorA++;
    }
    else
    {
      XYSensorB[CountSensorB][0] = i;
      XYSensorB[CountSensorB][1] = PositionTable[i];
      CountSensorB++;
    }
  }

  /*
  //Print results
  Serial.println("SensorA");
  for (byte i = 0; i < CountSensorA; i++)
  {
    Serial.print(XYSensorA[i][0]);
    Serial.print(",");
    Serial.println(XYSensorA[i][1]);
  }
  Serial.println("SensorB");
  for (byte i = 0; i < CountSensorB; i++)
  {
    Serial.print(XYSensorB[i][0]);
    Serial.print(",");
    Serial.println(XYSensorB[i][1]);
  }
  */

  //Find the wrap around value for SensorB
  for (byte i = CountSensorB; i > 0; i--)
  {
    //Modify time based on wrap around
    XYSensorB[i][0] = XYSensorB[i][0] - 60;

    //Check for end or warap around
    if ((XYSensorB[i-1][1] - XYSensorB[i][1]) < 0)
    {
      WrapAroundVal = XYSensorB[i][0] + 59;
      break;
    }
  }

  /*
  //Print results
  Serial.println("Modified SensorB data");
  for (byte i = 0; i < CountSensorB; i++)
  {
    Serial.print(XYSensorB[i][0]);
    Serial.print(",");
    Serial.println(XYSensorB[i][1]);
  }
  Serial.println(WrapAroundVal);
  */
  
  //Line fit sensor data
  double SensorALine[2];
  double SensorBLine[2];
  LineFitLSR(XYSensorA,SensorALine,CountSensorA);
  LineFitLSR(XYSensorB,SensorBLine,CountSensorB);

  //Calculate SensorA offset
  OffsetSensorA = round(SensorBLine[1]-SensorALine[1]);

  //Print results
  Serial.println("Line fit results");
  Serial.print("SensorA EQ: ");
  Serial.print(SensorALine[0]);
  Serial.print(",");
  Serial.println(SensorALine[1]);
  Serial.print("SensorB EQ: ");
  Serial.print(SensorBLine[0]);
  Serial.print(",");
  Serial.println(SensorBLine[1]);
  Serial.print("Offset: ");
  Serial.println(OffsetSensorA);

  //Offset SensorA readings
  for(byte i=0; i<CountSensorA; i++)
  {
    XYSensorA[i][1] = XYSensorA[i][1]+OffsetSensorA;
  }

  /*
  //Print results
  Serial.println("Shifted SensorA readings");
  for (byte i = 0; i < CountSensorA; i++)
  {
    Serial.print(XYSensorA[i][0]);
    Serial.print(",");
    Serial.println(XYSensorA[i][1]);
  }
  */

  //Combine modified SensorA and SensorB data (overwrite XYSensorA)
  CountSensorB = 0;
  for (byte i=CountSensorA; i<60; i++)
  {
    XYSensorA[i][0] = XYSensorB[CountSensorB][0];
    XYSensorA[i][1] = XYSensorB[CountSensorB][1];
    CountSensorB++;
  }

  /*
  //Print results
  Serial.println("Combined modified SensorA and SensorB values");
  for (byte i = 0; i < 60; i++)
  {
    Serial.print(XYSensorA[i][0]);
    Serial.print(",");
    Serial.println(XYSensorA[i][1]);
  }
  */

  //Line fit all the points
  LineFitLSR(XYSensorA,SensorALine,60);
  Slope = SensorALine[0];
  Intercept = SensorALine[1];

  //Print results
  Serial.println("Calibration results");
  Serial.print("Slope: ");
  Serial.println(Slope);
  Serial.print("Intercept: ");
  Serial.println(Intercept);
  Serial.print("OffsetSensorA: ");
  Serial.println(OffsetSensorA);
}

/*
***** ROLL THE CREDITS *****
  >> ReadVcc <<
  * Adjust VCC pin reading (didn't use)    https://forum.arduino.cc/index.php?topic=435065.0 
  * Use VCC pin to read voltage            https://provideyourown.com/2012/secret-arduino-voltmeter-measure-battery-voltage/

  >> ActivateSleep <<
  * Wake Arduino with interrupts     https://forum.arduino.cc/index.php?topic=435065.0 
 
***** Thanks everyone! *****
*/

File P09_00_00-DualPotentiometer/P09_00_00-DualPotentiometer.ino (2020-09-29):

//Define pins
#define PotA    A1 //Potentiometer A output
#define PotB    A2 //Potentiometer B output

//Global variables (Potentiometer Functions)
int ValSensorA;
int ValSensorB;

//Filter settings
int ArrayPotA[20];
int ArrayPotB[20];


void setup() {
  //Serial
  Serial.begin(9600);
}

void loop() {
  SensorSTD(20);
}

void SensorSTD(int Ct)
{
  //Aquire Ct points for both sensors
  for(int i=0; i<Ct; i++)
  {
    ArrayPotA[i] = analogRead(PotA);
    ArrayPotB[i] = analogRead(PotB);
  }

  //Sum of squares
  long SumSqA = 0;
  long SumSqB = 0;
  long TotA = 0;
  long TotB = 0;
  long tempA, tempB;
  for(int i=0; i<Ct; i++)
  {
    SumSqA += pow(ArrayPotA[i], 2);
    SumSqB += pow(ArrayPotB[i], 2);
    TotA += ArrayPotA[i];
    TotB += ArrayPotB[i];
    
    Serial.print(ArrayPotA[i]);
    Serial.print(",");
    Serial.println(ArrayPotB[i]);
  }
  TotA = pow(TotA, 2);
  TotB = pow(TotB, 2);
  TotA = TotA/Ct;
  TotB = TotB/Ct;

  int ResA = SumSqA-TotA;
  int ResB = SumSqB-TotB;

  Serial.println("");
  Serial.print(SumSqA);
  Serial.print(",");
  Serial.println(SumSqB);
  Serial.print(TotA);
  Serial.print(",");
  Serial.println(TotB);
  Serial.print(ResA);
  Serial.print(",");
  Serial.println(ResB);
  delay(5000);
}

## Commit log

2020-06-29 Add CAD Files
    [P09_00_00R1BeaconBase.FCStd, P09_00_00R1BeaconLens.FCStd, P09_00_00R1LEDMount.FCStd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]
2020-06-30 Modify CAD files
    [P09_00_00R1BeaconBase.FCStd, P09_00_00R1BeaconBase.stl, P09_00_00R1BeaconLens.stl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]
2020-06-30 Modify CAD
    [P09_00_00R1BeaconBase.FCStd, P09_00_00R1BottomPlate.FCStd, P09_00_00R1DriveGear.FCStd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]
2020-07-03 CAD updates
    [P09_00_00R1BeaconBase.FCStd, P09_00_00R1BeaconBase.stl, P09_00_00R1BeaconLens.FCStd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]
2020-07-06 CAD modifications
    [P09_00_00R2BeaconBase.FCStd, P09_00_00R2BeaconBase.stl, P09_00_00R2BottomPlate.FCStd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]
2020-07-09 Add P09_00_02 CAD
    [P09_00_00R2BeaconBase.FCStd, P09_00_02R1Build.FCStd, P09_00_02R1GearboxBottom.FCStd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]
2020-07-10 Reorganize files add new CAD design
    [P09_00_00R1BeaconBase.FCStd, P09_00_00R1BeaconBase.stl, P09_00_00R1BeaconLens.FCStd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]
2020-07-13 Organize CAD files
    [P09_00_00R1BeaconLens.FCStd, P09_00_00R1LEDMount.FCStd, P09_00_00R2BeaconBase.FCStd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]
2020-07-13 Reorganize CAD
    [P09_00_00R1BeaconBase.FCStd, P09_00_00R1BeaconLens.FCStd, P09_00_00R1BottomPlate.FCStd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]
2020-07-16 Testing motor control
    [Double Pot.ods]
2020-07-16 Working on double encoder
2020-07-21 Added positioning based on unknown and start nap
    [DualPotentiometerCalibration.ods]
2020-07-22 Soldered connections + minor changes
2020-07-22 Added calibration sequence
    [DualPotentiometerCalibration.ods]
2020-07-23 Working on motion path
    [DualPotentiometerCalibration.ods]
2020-07-23 Movement tests
    [DualPotentiometerCalibration.ods]
2020-07-24 New encoder idea
    [P09_00_04R1Encoder.FCStd, P09_00_04R1EncoderTop.FCStd, P09_00_04R1MainFrame.FCStd]
2020-08-31 Design P09_00_05
    [P09_00_05R1EncoderTop.FCStd, P09_00_05R1MainFrame.FCStd, a.stl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]
2020-09-16 Hall sensor tests
    [HallOutput.ods, P09_00_05R3EncoderTop.FCStd]
2020-09-23 Update P09_00_00-HallTest.ino
    No Filter mode
